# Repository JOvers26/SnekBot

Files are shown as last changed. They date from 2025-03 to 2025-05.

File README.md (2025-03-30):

# SnekBot

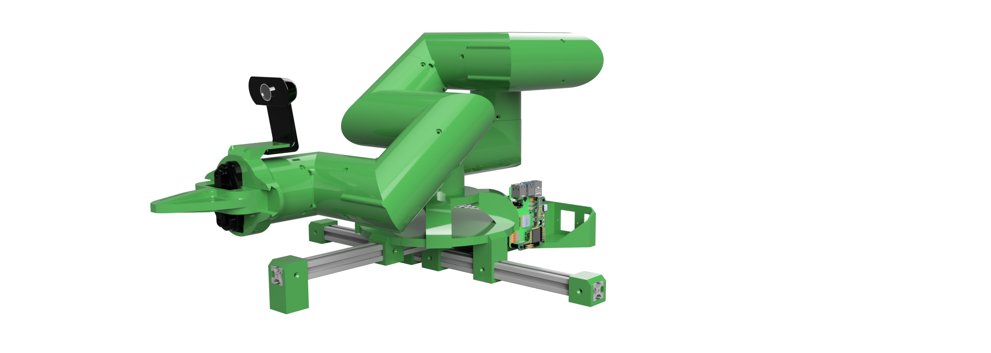
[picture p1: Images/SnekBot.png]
SnekBot Arm


## Six-Axis Robotic Arm and Control System for ROAR Lunar Surface Operations
This project is a work in progress and setup is subject to change.

## Project Summary
SnekBot is a six-axis robotic arm designed for the QUT ROAR team to use in the Australian Rover Challenge (ARCh)

## Installation & Setup
### Initial Steps
Ensure Ubuntu 24.04 is flashed on the Raspberry Pi 5 and configured for remote access via SSH.

## ROS2 Jazzy
### **1. Set Locale**
Ensure your system uses **UTF-8** encoding:
```sh
locale  # Check for UTF-8

sudo apt update && sudo apt install locales
sudo locale-gen en_US en_US.UTF-8
sudo update-locale LC_ALL=en_US.UTF-8 LANG=en_US.UTF-8
export LANG=en_US.UTF-8

locale  # Verify settings
```

### **2. Enable Required Repositories**
```sh
sudo apt install software-properties-common
sudo add-apt-repository universe
```

### **3. Add ROS 2 GPG Key**
```sh
sudo apt update && sudo apt install curl -y
sudo curl -sSL https://raw.githubusercontent.com/ros/rosdistro/master/ros.key -o /usr/share/keyrings/ros-archive-keyring.gpg
```

### **4. Add ROS 2 Repository**
```sh
echo "deb [arch=$(dpkg --print-architecture) signed-by=/usr/share/keyrings/ros-archive-keyring.gpg] http://packages.ros.org/ros2/ubuntu $(. /etc/os-release && echo $UBUNTU_CODENAME) main" | sudo tee /etc/apt/sources.list.d/ros2.list > /dev/null
```

### **5. Install Development Tools (Optional)**
```sh
sudo apt update && sudo apt install ros-dev-tools
```

### **6. Update Repository Caches**
```sh
sudo apt update
```

### **7. Upgrade System**
```sh
sudo apt upgrade
```

### **8. Install ROS 2 Jazzy Base**
```sh
sudo apt install ros-jazzy-ros-base
```

### **9. Setup Environment**
Ensure ROS 2 is sourced correctly:
```sh
# Replace ".bash" with your shell if you're not using Bash
# Possible values: setup.bash, setup.sh, setup.zsh
source /opt/ros/jazzy/setup.bash
```
For more details, visit the [official ROS 2 documentation](https://docs.ros.org/en/jazzy/Installation/Ubuntu-Install-Debs.html).

## Setting up SnekBot Project
### **1. Clone the repository**
```sh
git clone https://github.com/JOvers26/SnekBot
cd ~/SnekBot
```

### **2. Install dependencies**
```sh
cd ~/SnekBot/ros2_ws
sudo rosdep init
rosdep update
rosdep install --from-paths src --ignore-src -r -y
```

### **3. Install FOXGLOVE Monitoring (Optional)**
```sh
source /opt/ros/jazzy/setup.bash
sudo apt install ros-$ROS_DISTRO-foxglove-bridge
```

### **4. Build the ROS2 Workspace:**
```sh
cd ~SnekBot/ros2_ws
colcon build --symlink-install
source install/setup.bash
```

## Setting up ESP-IDF
### **1. Install Prerequisites**
```sh
sudo apt-get install git wget flex bison gperf python3 python3-pip python3-venv cmake ninja-build ccache libffi-dev libssl-dev dfu-util libusb-1.0-0
```

### **2. Get ESP-IDF**
```sh
mkdir -p ~/esp
cd ~/esp
git clone -b v5.2.5 --recursive https://github.com/espressif/esp-idf.git
```

### **3. Set up the Tools**
```sh
cd ~/esp/esp-idf
./install.sh all
```

### **4. Set up the Environment Variables**
```sh
. $HOME/esp/esp-idf/export.sh
```

### **5. Configure ESP32S3**
```sh
cd ~SnekBot/ESP32_Code/int32_Publisher
pip3 install catkin_pkg lark-parser colcon-common-extensions empy==3.3.4
idf.py set-target esp32s3
idf.py menuconfig

#In micro-ROS Settings ->
  #Set micro-ROS-Agent IP
  #Set WiFi Credentials
```

### **6. Build and flash software**
```sh
idf.py build
idf.py -p /dev/ttyACM0 flash

# Note if this does not work you may need to add user to the dialout group
sudo usermod -aG dialout $USER

idf.py -p /dev/ttyACM0 flash
```

## Install VSCode on Ubuntu
### **1. Install Prerequisites**
```sh
sudo apt-get install wget gpg
wget -qO- https://packages.microsoft.com/keys/microsoft.asc | gpg --dearmor > packages.microsoft.gpg
sudo install -D -o root -g root -m 644 packages.microsoft.gpg /etc/apt/keyrings/packages.microsoft.gpg
echo "deb [arch=amd64,arm64,armhf signed-by=/etc/apt/keyrings/packages.microsoft.gpg] https://packages.microsoft.com/repos/code stable main" |sudo tee /etc/apt/sources.list.d/vscode.list > /dev/null
rm -f packages.microsoft.gpg
sudo apt install apt-transport-https
sudo apt update
sudo apt install code # or code-insiders
```

## Setting up Robotics Toolbox Python environment
### **1. Install Prerequisites**
```sh
sudo apt install python3-venv
cd ~SnekBot
python3 -m venv venv
source venv/bin/activate

pip3 install pygame
pip3 install setuptools
pip3 install roboticstoolbox-python
pip3 install "numpy<2"
```

## Useful Commands
### **Sourcing Ros2**
```sh
source /opt/ros/jazzy/setup.bash
```

### **Building micro-ROS-Agent**
```sh
cd ~SnekBot/ros2_ws
colcon build --symlink-install
source install/setup.bash
```
```sh
ros2 run micro_ros_agent micro_ros_agent udp4 --port 8888
```

### **Launching Foxglove Monitoring**
```sh
source /opt/ros/jazzy/setup.bash
ros2 run foxglove_bridge foxglove_bridge
```

### **Sourcing ESP-IDF**
```sh
. $HOME/esp/esp-idf/export.sh
```

### **Flashing and Monitoring ESP32-S3**
```sh
idf.py -p /dev/ttyACM0 flash
idf.py -p /dev/ttyACM0 monitor
```

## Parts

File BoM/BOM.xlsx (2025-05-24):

Floor Mounted SnekBot
BoM Level | Part | Description | Pcs | Pcs / Unit | Unit Cost | Cost | Total Cost | Link
1 | 6813-2RS 65X85X10mm | Deep Groove Ball Bearings | 6 | 2 | $16.79 | $50.37 | $50.37 | https://www.aliexpress.com/item/1005007420073930.html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
2 | M3 x 50Pieces | M3 10mm Allen Bolt Screw | 120 | 50 | $1.57 | $3.77 | $4.71 | https://www.aliexpress.com/item/4000981220901.html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
3 | M4 x 20Pieces | M4 10mm Allen Bolt Screw | 24 | 20 | $1.57 | $1.88 | $3.14 | https://www.aliexpress.com/item/4000981220901.html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
4 | 150KG 12V DS51150 | 150Kg Servo | 6 | 1 | $32.99 | $197.94 | $197.94 | https://www.aliexpress.com/item/1005006215742647.html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
5 | ZIQIAN | 1080P Webcam | 1 | 1 | $24.89 | $24.89 | $24.89 | https://www.amazon.com.au/dp/B07VL7BNLZ?ref=ppx_yo2ov_dt_b_fed_asin_title&th=1
6 | 606-6x17x6mm | End Effector Bearings | 4 | 10 | $4.54 | $1.82 | $4.54 | https://www.aliexpress.com/item/4000909583668.html?scm_id=1007.14452.398466.0&scm-url=1007.14452.398466.0
7 | C14 Locked S8B | Power Supply Docking Outlet | 1 | 1 | $2.14 | $2.14 | $2.14 | https://www.aliexpress.com/item/1005001515720134.html?src=google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
8 | KCD3 3PIN Black | Power Supply Rocker Switch | 1 | 1 | $1.66 | $1.66 | $1.66 | https://www.aliexpress.com/item/1005005681017616.html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
9 | 12V 15A 180W | 180W Power Supply Adapter Transformer | 1 | 1 | $21.39 | $21.39 | $21.39 | https://www.amazon.com.au/dp/B0986LNBW8?ref=ppx_yo2ov_dt_b_fed_asin_title&th=1
10 | Raspberry Pi | 5 Model B 16GB | 1 | 1 | $212.50 | $212.50 | $212.50 | https://core-electronics.com.au/raspberry-pi-5-model-b-16gb.html
11 | USB C Cable | 15cm | 1 | 1 | $9.71 | $9.71 | $9.71 | https://www.amazon.com.au/dp/B01CZVEUIE?ref=ppx_yo2ov_dt_b_fed_asin_title&th=1
12 | XT60 Connectors | Male - Female Pair | 7 | 5 | $13.71 | $19.19 | $27.42 | https://www.aliexpress.com/w/wholesale-XT%2525252d60-XT60-Male-Female.html
13 | Light Duty Hook-up Wire | 26 AWG Pack | 1 | 8 | $39.95 | $4.99 | $39.95 | https://www.jaycar.com.au/light-duty-hook-up-wire-pack-8-colours/p/WH3009
14 | Power Wire (Black) | 16 AWG (5 meter) | 1 | 1 | $1.57 | $1.57 | $1.57 | https://www.aliexpress.com/item/1005006064722016.html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
15 | Power Wire (Red) | 16 AWG (5 meter) | 1 | 1 | $1.57 | $1.57 | $1.57 | https://www.aliexpress.com/item/1005006064722016.html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
16 | Dupont Connector 2.54mm | Dupont Cable Jumper Wire Pin Header Housing Kit | 1 | 1 | $1.57 | $1.57 | $1.57 | https://www.aliexpress.com/item/33011610420.html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
17 | LM2596 | DC to DC Buck Converter | 2 | 5 | $8.01 | $3.20 | $8.01 | https://www.aliexpress.com/item/1005007331564532.html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
18 | 2020 Extrusion | 450MM | 2 | 1 | $13.59 | $27.18 | $27.18 | https://www.aliexpress.com/item/1005002645411058.html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
19 | M3 x 20Pieces | 20 Series Slot T-nut Sliding T Nut | 20 | 20 | $3.49 | $3.49 | $3.49 | https://www.aliexpress.com/item/32814359094.html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
20 | 1x20kg 180 Arm | End Effector Servo Motor | 1 | 1 | $10.40 | $10.40 | $10.40 | https://www.aliexpress.com/item/1005007532136781.html?scm_id=1007.40196.436742.0&scm-url=1007.40196.436742.0
21 | 356-EP32S3WROOM1N8R8 | ESP32-S3 | 1 | 1 | $5.68 | $5.68 | $5.68 | https://au.mouser.com/ProductDetail/356-EP32S3WROOM1N8R8
22 | SKRKAHE020 | ESP32 Control Buttons | 2 | 1 | $0.91 | $1.82 | $1.82 | https://au.mouser.com/ProductDetail/688-SKRKAHE010
23 | 640-USB4105-GF-A | USBC Connector | 1 | 1 | $1.01 | $1.01 | $1.01 | https://au.mouser.com/ProductDetail/640-USB4105-GF-A
24 | 926-LM1117MPX3.3NOPB | Volatge Regulator | 1 | 1 | $1.43 | $1.43 | $1.43 | https://au.mouser.com/ProductDetail/926-LM1117MPX3.3NOPB
25 | 581-MP01EA045 | Diode | 1 | 1 | $0.83 | $0.83 | $0.83 | https://au.mouser.com/ProductDetail/581-MP01EA045
26 | 667-ERJ-UP6D5101V | 5.1KOhm Resistors | 3 | 1 | $0.23 | $0.69 | $0.69 | https://au.mouser.com/ProductDetail/667-ERJ-UP6D5101V
27 | 581-KGM21AR71A106KU | 10uF Capacitor | 2 | 1 | $0.46 | $0.93 | $0.93 | https://au.mouser.com/ProductDetail/581-KGM21AR71A106KU
28 | 963-LMK212SD104KG-T | 0.1uF Capacitor | 3 | 1 | $0.46 | $1.39 | $1.39 | https://au.mouser.com/ProductDetail/963-LMK212SD104KG-T
29 | PCD | JLCPCB | 1 | 5 | $20.00 | $4.00 | $20.00 | https://jlcpcb.com/?from=VGB_AU&adgroupid=172970581377&gad_source=1&gbraid=0AAAAACUKBgRO7FoYKeTPkvkSdP2pwtPFG
30 | eSUN PLA+ 3D Filament | 2.85mm 1kg | 2 | 1 | $25.95 | $51.90 | $51.90 | https://cubictech.com.au/products/esun-pla-3d-filament-2-85mm-1kg?variant=40317601865
30 | xbox Controller |  | 1 | 1 | $89 | $89.00 | $89.00 | https://www.amazon.com.au/Xbox-Wireless-Controller-Carbon-Black/dp/B08K3FVP5N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
Totals |  |  |  |  |  | $759.92 | $828.83
Snekbot Only |  |  |  |  |  | $439.18 | $492.09

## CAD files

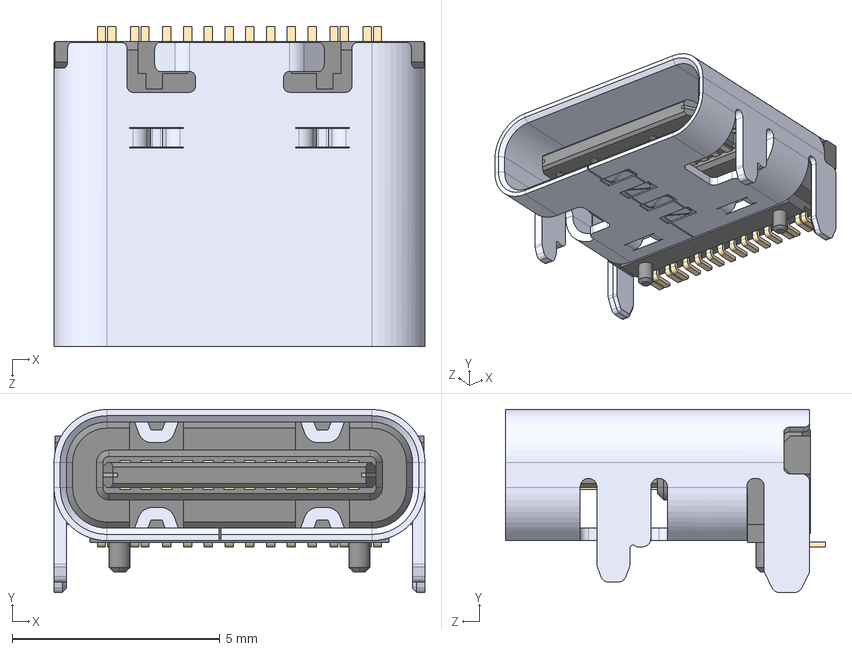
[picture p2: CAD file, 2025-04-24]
ESP32 PCB/USB4105-GF-A/USB4105-GF-A.step
8.94 x 4.41 x 7.71 mm

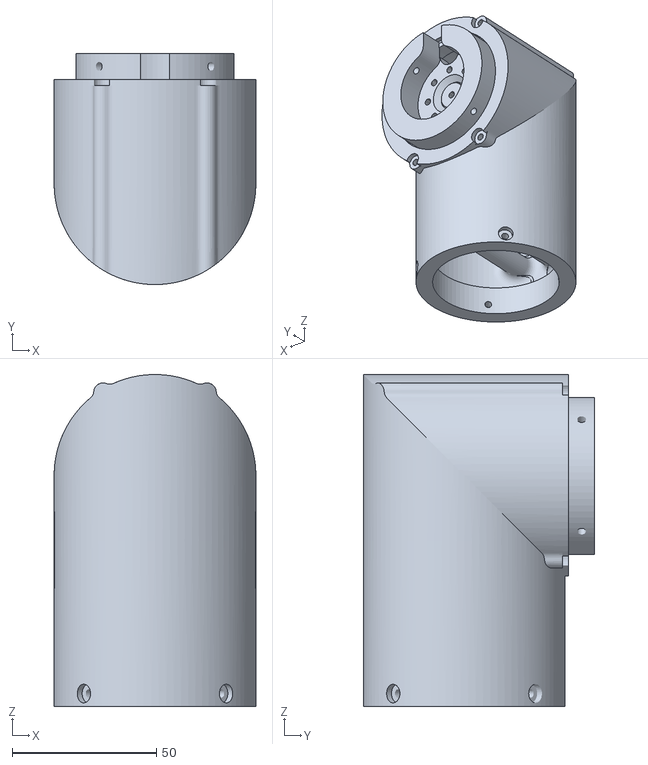
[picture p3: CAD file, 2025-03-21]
RaspberryPi_Code/SnekBot_URDF/meshes/Joint0.stl
70.0 x 80.2 x 115.2

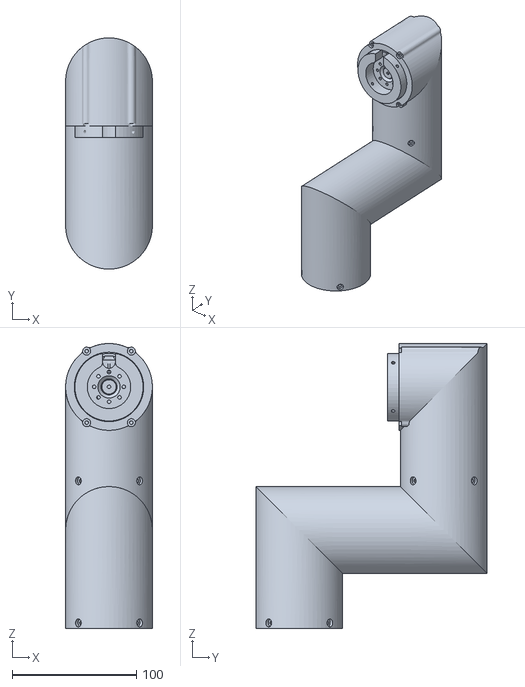
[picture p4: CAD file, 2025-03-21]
RaspberryPi_Code/SnekBot_URDF/meshes/Joint3.stl
70.0 x 186.4 x 229.8

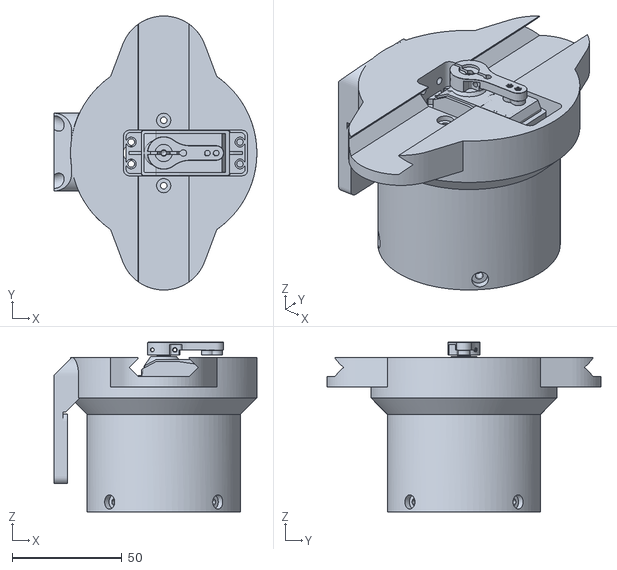
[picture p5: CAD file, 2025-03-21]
RaspberryPi_Code/SnekBot_URDF/meshes/Joint5.stl
92.5 x 125.0 x 77.4

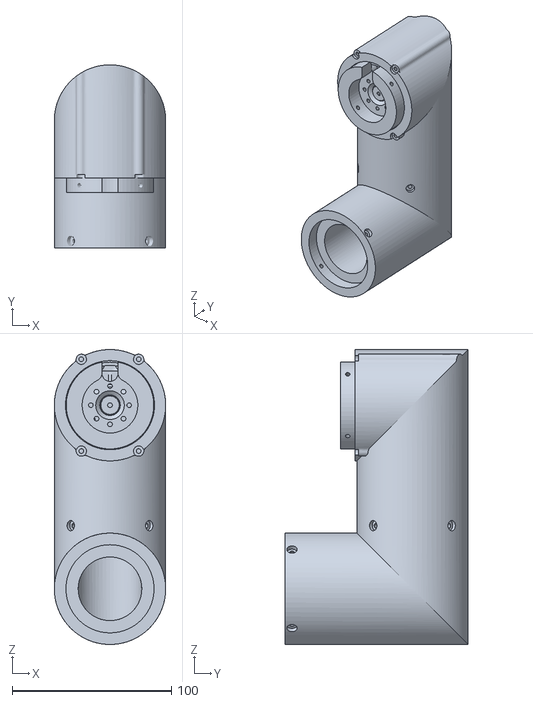
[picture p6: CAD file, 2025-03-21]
RaspberryPi_Code/SnekBot_URDF/meshes/Joint1.stl
70.0 x 115.2 x 185.4

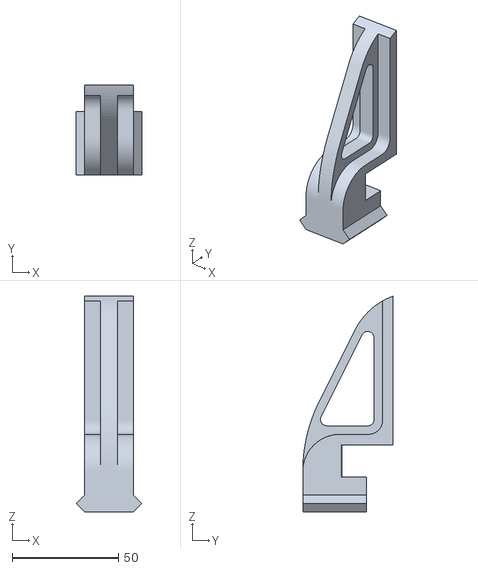
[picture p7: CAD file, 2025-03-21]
RaspberryPi_Code/SnekBot_URDF/meshes/Left-Gripper.stl
31.0 x 42.5 x 101.5

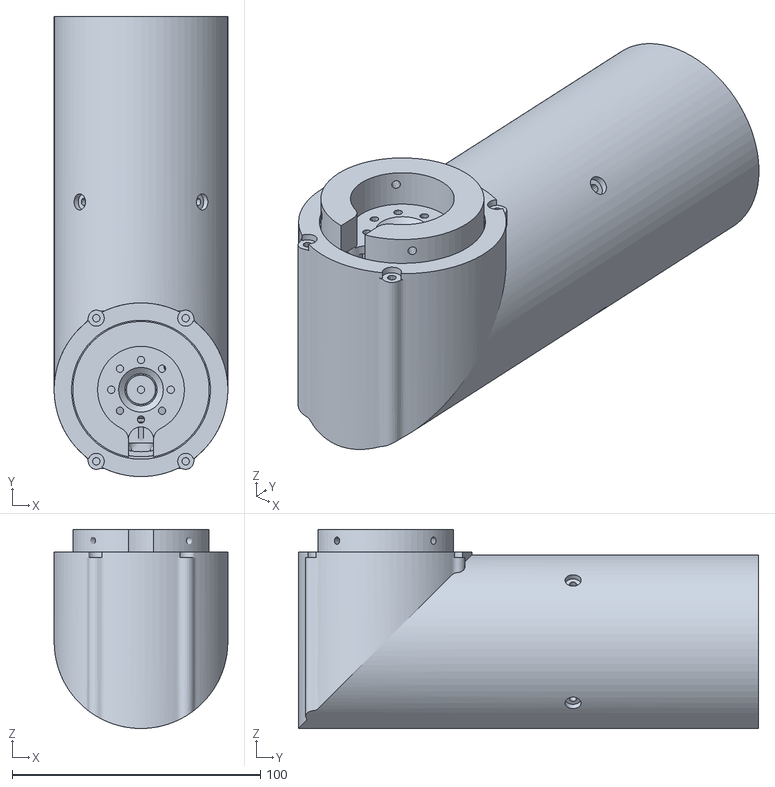
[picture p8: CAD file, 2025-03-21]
RaspberryPi_Code/SnekBot_URDF/meshes/Base.stl
70.0 x 185.5 x 80.2

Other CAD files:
RaspberryPi_Code/SnekBot_URDF/meshes/Joint2.stl
RaspberryPi_Code/SnekBot_URDF/meshes/Joint4.stl
RaspberryPi_Code/SnekBot_URDF/meshes/Right-Gripper.stl

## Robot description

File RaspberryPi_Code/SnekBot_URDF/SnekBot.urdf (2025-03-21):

<?xml version='1.0' encoding='utf-8'?>
<robot name="SnekBot">
    <link name="Joint4">
        <inertial>
            <origin xyz="-7.31917079953468e-07 -0.002720965823309811 -0.06094824846597635" rpy="0.0 9.921302603843483e-48 0.0" />
            <mass value="2.170299150249054" />
            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
        </inertial>
        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
    </link>
    <link name="Joint3">
        <inertial>
            <origin xyz="1.4095052347553083e-07 -0.06948927422346683 -0.1036765010036558" rpy="0.0 -0.0 1.302943823802202e-60" />
            <mass value="6.860254512476634" />
            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
        </inertial>
        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
    </link>
    <link name="Joint2">
        <inertial>
            <origin xyz="-7.319170719899921e-07 -0.0027209737564369975 -0.060948248465979474" rpy="3.944304526105059e-31 2.8562667779245755e-62 9.723461371658036e-63" />
            <mass value="2.170299150249074" />
            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
        </inertial>
        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
    </link>
    <link name="Joint1">
        <inertial>
            <origin xyz="3.744606777828738e-07 0.04699627745454283 -0.0685629731482273" rpy="0.0 -0.0 0.0" />
            <mass value="4.508264373489419" />
            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
        </inertial>
        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
    </link>
    <link name="Joint0">
        <inertial>
            <origin xyz="-7.319170712847745e-07 -0.002720973756436303 -0.06094825459578699" rpy="0.0 -0.0 0.0" />
            <mass value="2.1702991502490603" />
            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
        </inertial>
        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
    </link>
    <link name="Base">
        <inertial>
            <origin xyz="-4.1041387313046547e-07 -0.020138795421307955 0.037548882045009294" rpy="0.0 0.0 0.0" />
            <mass value="3.812666297852429" />
            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
        </inertial>
        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
    </link>
    <link name="Joint5">
        <inertial>
            <origin xyz="-0.0025494513129547705 -7.658363454307156e-06 -0.04525477560826317" rpy="0.0 -0.0 -1.1973985901296076e-48" />
            <mass value="1.7334916519714307" />
            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
        </inertial>
        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
    </link>
    <joint name="Base_Revolute-0" type="revolute">
        <origin xyz="-5.742377618504593e-17 -0.07946200000000023 0.035" rpy="3.141592653589793 0 0" />
        <parent link="Base" />
        <child link="Joint0" />
        <axis xyz="0 0 1" />
        <limit lower="-2.356194" upper="2.356194" effort="87" velocity="2.175" />
    </joint>
    <joint name="Joint0_Revolute-1" type="revolute">
        <origin xyz="-6.192261280341597e-50 -0.036199999999999996 -0.0802" rpy="-1.5707963267948952 0 0" />
        <parent link="Joint0" />
        <child link="Joint1" />
        <axis xyz="0 0 1" />
        <limit lower="-2.356194" upper="2.356194" effort="87" velocity="2.175" />
    </joint>
    <joint name="Joint1_Revolute-2" type="revolute">
        <origin xyz="7.592786212752303e-33 0.11539999999999996 -0.04400000000000016" rpy="-3.1415926535897922 0 0" />
        <parent link="Joint1" />
        <child link="Joint2" />
        <axis xyz="0 0 1" />
        <limit lower="-2.356194" upper="2.356194" effort="87" velocity="2.175" />
    </joint>
    <joint name="Joint2_Revolute-3" type="revolute">
        <origin xyz="5.123092549358938e-32 -0.036200000000000225 -0.08019999999999991" rpy="-1.570796326794893 0 0" />
        <parent link="Joint2" />
        <child link="Joint3" />
        <axis xyz="0 0 1" />
        <limit lower="-2.356194" upper="2.356194" effort="87" velocity="2.175" />
    </joint>
    <joint name="Joint3_Revolute-4" type="revolute">
        <origin xyz="1.1040657277305825e-14 -0.0802000000000012 -0.19479999999999947" rpy="1.5707963267948506 0 0" />
        <parent link="Joint3" />
        <child link="Joint4" />
        <axis xyz="0 0 1" />
        <limit lower="-2.356194" upper="2.356194" effort="87" velocity="2.175" />
    </joint>
    <joint name="Joint4_Revolute-5" type="revolute">
        <origin xyz="1.8787416067335387e-15 -0.036199999999996846 -0.08020000000000144" rpy="-1.570796326794869 0 0" />
        <parent link="Joint4" />
        <child link="Joint5" />
        <axis xyz="0 0 1" />
        <limit lower="-2.356194" upper="2.356194" effort="87" velocity="2.175" />
    </joint>
</robot>

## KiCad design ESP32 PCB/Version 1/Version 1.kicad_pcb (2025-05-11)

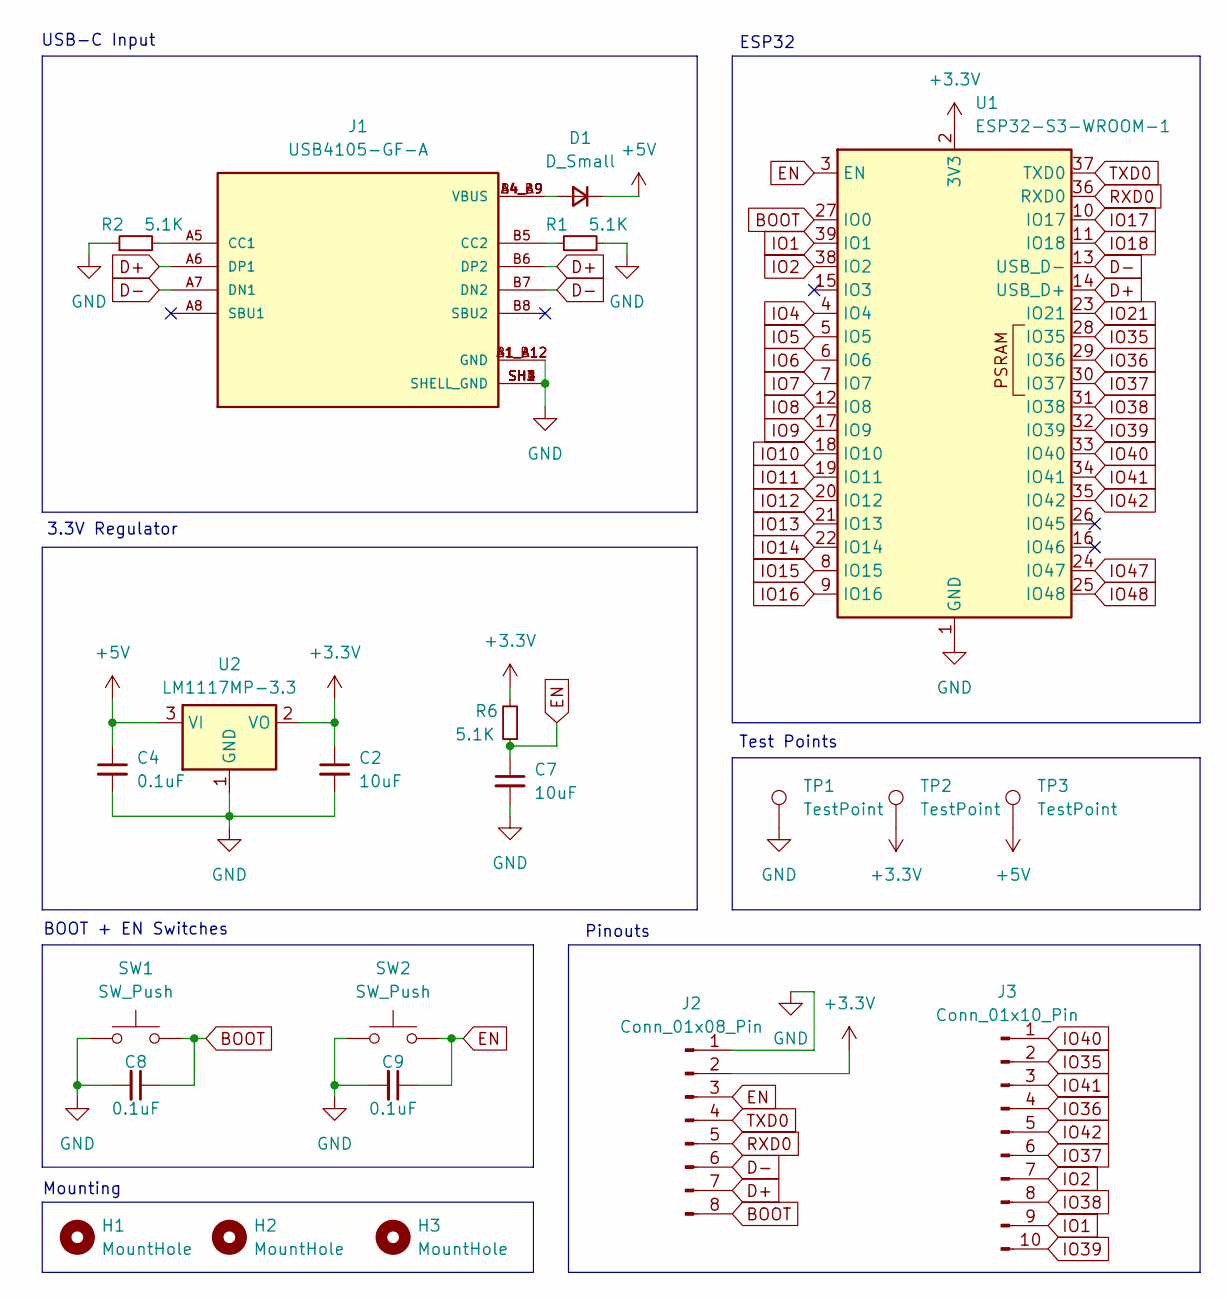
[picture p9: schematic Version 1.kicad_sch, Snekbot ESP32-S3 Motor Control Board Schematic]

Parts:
C2, C7: 10uF; C_0805_2012Metric_Pad1.18x1.45mm_HandSolder
C4, C8, C9: 0.1uF; C_0805_2012Metric_Pad1.18x1.45mm_HandSolder
D1: D_Small; D_0805_2012Metric_Pad1.15x1.40mm_HandSolder
H1, H2, H3: MountHole; MountingHole_3.2mm_M3
J1: USB4105-GF-A; GCT_USB4105-GF-A; PARTREV B4
J2: Conn_01x08_Pin; PinHeader_1x08_P2.54mm_Vertical
J3: Conn_01x10_Pin; PinHeader_2x05_P2.54mm_Vertical
R1, R2, R6: 5.1K; R_0805_2012Metric_Pad1.20x1.40mm_HandSolder
SW1, SW2: SW_Push; SW_Push_SPST_NO_Alps_SKRK
TP1, TP2, TP3: TestPoint; TestPoint_Pad_D3.0mm
U1: ESP32-S3-WROOM-1
U2: LM1117MP-3.3; SOT-223-3_TabPin2

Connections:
+3.3V: C2.1, J2.2, R6.2, TP2.1, U1.2 (3V3), U2.2 (VO)
+5V: C4.1, D1.1 (K), TP3.1, U2.3 (VI)
BOOT: C8.1, J2.8, SW1.2, U1.27 (IO0)
D+: J1.A6 (DP1), J1.B6 (DP2), J2.7, U1.14 (USB_D+)
D-: J1.A7 (DN1), J1.B7 (DN2), J2.6, U1.13 (USB_D-)
EN: C7.1, C9.1, J2.3, R6.1, SW2.2, U1.3 (EN)
GND: C2.2, C4.2, C7.2, C8.2, C9.2, J1.A1_B12 (GND), J1.B1_A12 (GND), J1.SH1 (SHELL_GND), J1.SH2 (SHELL_GND), J1.SH3 (SHELL_GND), J1.SH4 (SHELL_GND), J2.1, R1.2, R2.1, SW1.1, SW2.1, TP1.1, U1.1 (GND), U1.40 (GND), U1.41 (GND), U2.1 (GND)
IO1: J3.9, U1.39 (IO1)
IO2: J3.7, U1.38 (IO2)
IO4: U1.4 (IO4)
IO5: U1.5 (IO5)
IO6: U1.6 (IO6)
IO7: U1.7 (IO7)
IO8: U1.12 (IO8)
IO9: U1.17 (IO9)
IO10: U1.18 (IO10)
IO11: U1.19 (IO11)
IO12: U1.20 (IO12)
IO13: U1.21 (IO13)
IO14: U1.22 (IO14)
IO15: U1.8 (IO15)
IO16: U1.9 (IO16)
IO17: U1.10 (IO17)
IO18: U1.11 (IO18)
IO21: U1.23 (IO21)
IO35: J3.2, U1.28 (IO35)
IO36: J3.4, U1.29 (IO36)
IO37: J3.6, U1.30 (IO37)
IO38: J3.8, U1.31 (IO38)
IO39: J3.10, U1.32 (IO39)
IO40: J3.1, U1.33 (IO40)
IO41: J3.3, U1.34 (IO41)
IO42: J3.5, U1.35 (IO42)
IO47: U1.24 (IO47)
IO48: U1.25 (IO48)
unnamed: D1.2 (A), J1.A4_B9 (VBUS), J1.B4_A9 (VBUS)
unnamed: J1.A5 (CC1), R2.2
unnamed: J1.B5 (CC2), R1.1
RXD0: J2.5, U1.36 (RXD0)
TXD0: J2.4, U1.37 (TXD0)

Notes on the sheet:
BOOT + EN Switches
3.3V Regulator
Mounting
Pinouts
USB-C Input
ESP32
Test Points

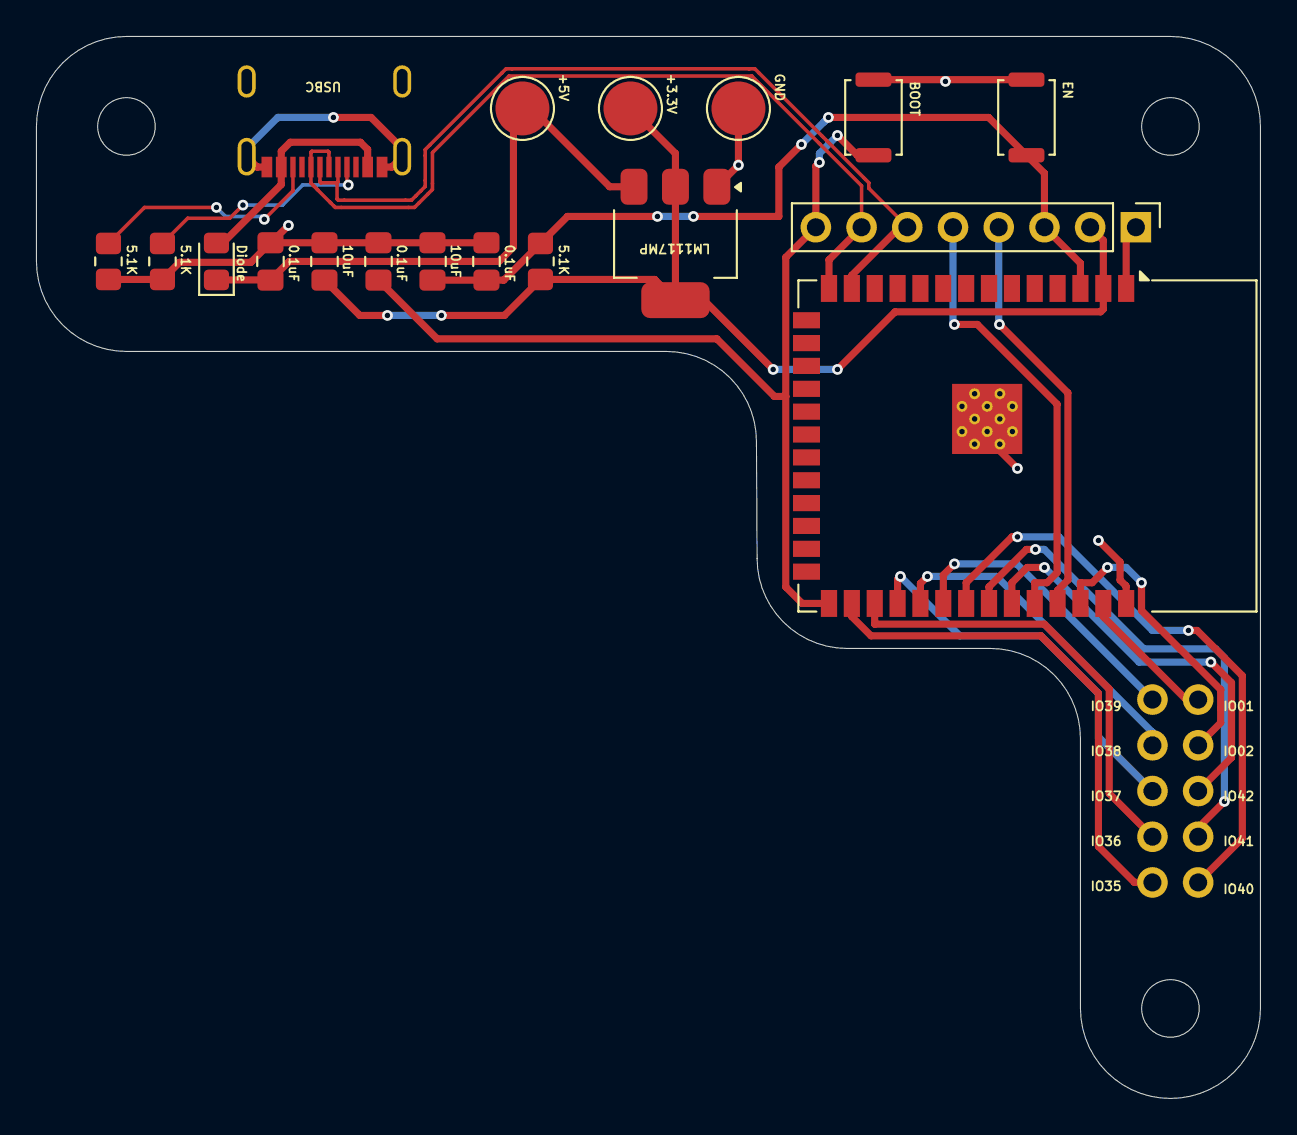
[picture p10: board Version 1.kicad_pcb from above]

Board: 2 copper layers, 68.0 x 59.0 mm, 22 parts (0 on the bottom side), 22 nets.

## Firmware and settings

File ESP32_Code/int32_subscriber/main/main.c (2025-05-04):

#include <string.h>
#include <stdio.h>
#include <unistd.h>
#include <stdlib.h>  // For malloc

#include "freertos/FreeRTOS.h"
#include "freertos/task.h"
#include "esp_log.h"
#include "esp_system.h"

#include <uros_network_interfaces.h>
#include <rcl/rcl.h>
#include <rcl/error_handling.h>
#include <sensor_msgs/msg/joint_state.h>
#include <rclc/rclc.h>
#include <rclc/executor.h>

#include "driver/mcpwm_prelude.h"
#include <math.h>

#ifdef CONFIG_MICRO_ROS_ESP_XRCE_DDS_MIDDLEWARE
#include <rmw_microros/rmw_microros.h>
#endif

#define NUM_JOINTS 7
#define RCCHECK(fn) { rcl_ret_t temp_rc = fn; if((temp_rc != RCL_RET_OK)){printf("Failed status on line %d: %d. Aborting.\n", __LINE__, (int)temp_rc); vTaskDelete(NULL);} }
#define RCSOFTCHECK(fn) { rcl_ret_t temp_rc = fn; if((temp_rc != RCL_RET_OK)){printf("Failed status on line %d: %d. Continuing.\n", __LINE__, (int)temp_rc);} }

// Subscription variable
rcl_subscription_t snekbot_joint_state_subscriber;
sensor_msgs__msg__JointState recv_joint_state_msg;

#define JOINT_1 1
#define JOINT_2 2
#define JOINT_3 42
#define JOINT_4 41
#define JOINT_5 40
#define JOINT_6 39
#define JOINT_G 38
#define SERVO_MIN_PULSEWIDTH_US 500 
#define SERVO_MAX_PULSEWIDTH_US 2500
#define SERVO_MAX_DEGREE 270
#define PI 3.14159265359

mcpwm_timer_handle_t timer0;
mcpwm_oper_handle_t operator0;
mcpwm_cmpr_handle_t comparator01;
mcpwm_cmpr_handle_t comparator02;
mcpwm_gen_handle_t generator01;
mcpwm_gen_handle_t generator02;

mcpwm_timer_handle_t timer1;
mcpwm_oper_handle_t operator1;
mcpwm_cmpr_handle_t comparator11;
mcpwm_cmpr_handle_t comparator12;
mcpwm_gen_handle_t generator11;
mcpwm_gen_handle_t generator12;

mcpwm_timer_handle_t timer2;
mcpwm_oper_handle_t operator2;
mcpwm_cmpr_handle_t comparator21;
mcpwm_cmpr_handle_t comparator22;
mcpwm_gen_handle_t generator21;
mcpwm_gen_handle_t generator22;

mcpwm_timer_handle_t timer3;
mcpwm_oper_handle_t operator3;
mcpwm_cmpr_handle_t comparator31;
mcpwm_gen_handle_t generator31;




static uint32_t radians_to_angle(float radians) {
    float angle = ((radians + M_PI) / (2 * M_PI)) * SERVO_MAX_DEGREE;
    
    if (angle < 0) angle = 0;
    if (angle > SERVO_MAX_DEGREE) angle = SERVO_MAX_DEGREE;
    
    return (uint32_t)angle;
}

static uint32_t angle_to_pulsewidth(uint32_t angle) {
    return SERVO_MIN_PULSEWIDTH_US + (angle * (SERVO_MAX_PULSEWIDTH_US - SERVO_MIN_PULSEWIDTH_US) / SERVO_MAX_DEGREE);
}

static void set_servo_angle_radians(mcpwm_cmpr_handle_t comparator, float radians) {
    uint32_t angle = radians_to_angle(radians);
    uint32_t pulse_width = angle_to_pulsewidth(angle);
    mcpwm_comparator_set_compare_value(comparator, pulse_width);
}

static void setup_pwm(void) {
    // Timer 0 setup (for JOINT_1, JOINT_2, JOINT_3)
    mcpwm_timer_config_t timer_config = {
        .group_id = 0,
        .clk_src = MCPWM_TIMER_CLK_SRC_DEFAULT,
        .resolution_hz = 1000000,  
        .count_mode = MCPWM_TIMER_COUNT_MODE_UP,
        .period_ticks = 20000  // 50Hz PWM
    };



    mcpwm_new_timer(&timer_config, &timer0);

    // Timer 1 setup (for JOINT_4, JOINT_5)
    mcpwm_new_timer(&timer_config, &timer1);

    // Timer 2 setup (for JOINT_6, JOINT_G)
    mcpwm_new_timer(&timer_config, &timer2);

    mcpwm_timer_config_t timer_config3 = {
        .group_id = 1,
        .clk_src = MCPWM_TIMER_CLK_SRC_DEFAULT,
        .resolution_hz = 1000000,  
        .count_mode = MCPWM_TIMER_COUNT_MODE_UP,
        .period_ticks = 20000  // 50Hz PWM
    };
    mcpwm_new_timer(&timer_config3, &timer3);

    // Operator setup for Timer 0
    mcpwm_operator_config_t operator_config = {.group_id = 0};
    mcpwm_new_operator(&operator_config, &operator0);
    mcpwm_operator_connect_timer(operator0, timer0);

    // Operator setup for Timer 1
    mcpwm_new_operator(&operator_config, &operator1);
    mcpwm_operator_connect_timer(operator1, timer1);

    // Operator setup for Timer 2
    mcpwm_new_operator(&operator_config, &operator2);
    mcpwm_operator_connect_timer(operator2, timer2);

    mcpwm_operator_config_t operator_config3 = {.group_id = 1};
    mcpwm_new_operator(&operator_config3, &operator3);
    mcpwm_operator_connect_timer(operator3, timer3);

    // Comparator and generator setup for each joint and timer

    // Timer 0 (for JOINT_1, JOINT_2, JOINT_3)
    // JOINT_1
    mcpwm_comparator_config_t comparator01_config = {.flags.update_cmp_on_tez = true};
    mcpwm_new_comparator(operator0, &comparator01_config, &comparator01);
    mcpwm_generator_config_t generator01_config = {
        .gen_gpio_num = JOINT_1,
        .flags.invert_pwm = false
    };
    mcpwm_new_generator(operator0, &generator01_config, &generator01);
    mcpwm_generator_set_action_on_timer_event(generator01,
        MCPWM_GEN_TIMER_EVENT_ACTION(MCPWM_TIMER_DIRECTION_UP, MCPWM_TIMER_EVENT_EMPTY, MCPWM_GEN_ACTION_HIGH));
    mcpwm_generator_set_action_on_compare_event(generator01,
        MCPWM_GEN_COMPARE_EVENT_ACTION(MCPWM_TIMER_DIRECTION_UP, comparator01, MCPWM_GEN_ACTION_LOW));

    // JOINT_2
    mcpwm_comparator_config_t comparator02_config = {.flags.update_cmp_on_tez = true};
    mcpwm_new_comparator(operator0, &comparator02_config, &comparator02);
    mcpwm_generator_config_t generator02_config = {
        .gen_gpio_num = JOINT_2,
        .flags.invert_pwm = false
    };
    mcpwm_new_generator(operator0, &generator02_config, &generator02);
    mcpwm_generator_set_action_on_timer_event(generator02,
        MCPWM_GEN_TIMER_EVENT_ACTION(MCPWM_TIMER_DIRECTION_UP, MCPWM_TIMER_EVENT_EMPTY, MCPWM_GEN_ACTION_HIGH));
    mcpwm_generator_set_action_on_compare_event(generator02,
        MCPWM_GEN_COMPARE_EVENT_ACTION(MCPWM_TIMER_DIRECTION_UP, comparator02, MCPWM_GEN_ACTION_LOW));


    // Timer 1 (for JOINT_4, JOINT_5)
    // JOINT_3
    mcpwm_comparator_config_t comparator11_config = {.flags.update_cmp_on_tez = true};
    mcpwm_new_comparator(operator1, &comparator11_config, &comparator11);
    mcpwm_generator_config_t generator11_config = {
        .gen_gpio_num = JOINT_3,
        .flags.invert_pwm = false
    };
    mcpwm_new_generator(operator1, &generator11_config, &generator11);
    mcpwm_generator_set_action_on_timer_event(generator11,
        MCPWM_GEN_TIMER_EVENT_ACTION(MCPWM_TIMER_DIRECTION_UP, MCPWM_TIMER_EVENT_EMPTY, MCPWM_GEN_ACTION_HIGH));
    mcpwm_generator_set_action_on_compare_event(generator11,
        MCPWM_GEN_COMPARE_EVENT_ACTION(MCPWM_TIMER_DIRECTION_UP, comparator11, MCPWM_GEN_ACTION_LOW));

    // JOINT_4
    mcpwm_comparator_config_t comparator12_config = {.flags.update_cmp_on_tez = true};
    mcpwm_new_comparator(operator1, &comparator12_config, &comparator12);
    mcpwm_generator_config_t generator12_config = {
        .gen_gpio_num = JOINT_4,
        .flags.invert_pwm = false
    };
    mcpwm_new_generator(operator1, &generator12_config, &generator12);
    mcpwm_generator_set_action_on_timer_event(generator12,
        MCPWM_GEN_TIMER_EVENT_ACTION(MCPWM_TIMER_DIRECTION_UP, MCPWM_TIMER_EVENT_EMPTY, MCPWM_GEN_ACTION_HIGH));
    mcpwm_generator_set_action_on_compare_event(generator12,
        MCPWM_GEN_COMPARE_EVENT_ACTION(MCPWM_TIMER_DIRECTION_UP, comparator12, MCPWM_GEN_ACTION_LOW));

    // Timer 2 (for JOINT_6, JOINT_G)
    // JOINT_5
    mcpwm_comparator_config_t comparator21_config = {.flags.update_cmp_on_tez = true};
    mcpwm_new_comparator(operator2, &comparator21_config, &comparator21);
    mcpwm_generator_config_t generator21_config = {
        .gen_gpio_num = JOINT_5,
        .flags.invert_pwm = false
    };
    mcpwm_new_generator(operator2, &generator21_config, &generator21);
    mcpwm_generator_set_action_on_timer_event(generator21,
        MCPWM_GEN_TIMER_EVENT_ACTION(MCPWM_TIMER_DIRECTION_UP, MCPWM_TIMER_EVENT_EMPTY, MCPWM_GEN_ACTION_HIGH));
    mcpwm_generator_set_action_on_compare_event(generator21,
        MCPWM_GEN_COMPARE_EVENT_ACTION(MCPWM_TIMER_DIRECTION_UP, comparator21, MCPWM_GEN_ACTION_LOW));

    // JOINT_6 (Gripper)
    mcpwm_comparator_config_t comparator22_config = {.flags.update_cmp_on_tez = true};
    mcpwm_new_comparator(operator2, &comparator22_config, &comparator22);
    mcpwm_generator_config_t generator22_config = {
        .gen_gpio_num = JOINT_6,
        .flags.invert_pwm = false
    };
    mcpwm_new_generator(operator2, &generator22_config, &generator22);
    mcpwm_generator_set_action_on_timer_event(generator22,
        MCPWM_GEN_TIMER_EVENT_ACTION(MCPWM_TIMER_DIRECTION_UP, MCPWM_TIMER_EVENT_EMPTY, MCPWM_GEN_ACTION_HIGH));
    mcpwm_generator_set_action_on_compare_event(generator22,
        MCPWM_GEN_COMPARE_EVENT_ACTION(MCPWM_TIMER_DIRECTION_UP, comparator22, MCPWM_GEN_ACTION_LOW));

    mcpwm_comparator_config_t comparator31_config = {.flags.update_cmp_on_tez = true};
    mcpwm_new_comparator(operator3, &comparator31_config, &comparator31);
    mcpwm_generator_config_t generator31_config = {
        .gen_gpio_num = JOINT_G,
        .flags.invert_pwm = false
    };
    mcpwm_new_generator(operator3, &generator31_config, &generator31);
    mcpwm_generator_set_action_on_timer_event(generator31,
        MCPWM_GEN_TIMER_EVENT_ACTION(MCPWM_TIMER_DIRECTION_UP, MCPWM_TIMER_EVENT_EMPTY, MCPWM_GEN_ACTION_HIGH));
    mcpwm_generator_set_action_on_compare_event(generator31,
        MCPWM_GEN_COMPARE_EVENT_ACTION(MCPWM_TIMER_DIRECTION_UP, comparator31, MCPWM_GEN_ACTION_LOW));

    // Start all timers
    mcpwm_timer_enable(timer0);
    mcpwm_timer_start_stop(timer0, MCPWM_TIMER_START_NO_STOP);
    
    mcpwm_timer_enable(timer1);
    mcpwm_timer_start_stop(timer1, MCPWM_TIMER_START_NO_STOP);
    
    mcpwm_timer_enable(timer2);
    mcpwm_timer_start_stop(timer2, MCPWM_TIMER_START_NO_STOP);

    mcpwm_timer_enable(timer3);
    mcpwm_timer_start_stop(timer3, MCPWM_TIMER_START_NO_STOP);
}


// Subscription callback function
void snekbot_joint_state_callback(const void * msgin)
{
    const sensor_msgs__msg__JointState * msg = (const sensor_msgs__msg__JointState *)msgin;

    if (msg == NULL) {
        printf("[ERROR] Received NULL message!\n");
        return;
    }

    printf("Received Joint States:\n");
    for (size_t i = 0; i < msg->position.size; i++) {
        printf("  Joint %zu (%s): %f\n", i, msg->name.data[i].data, msg->position.data[i]);
        if (strcmp(msg->name.data[i].data, "joint_1") == 0) {
            set_servo_angle_radians(comparator01, (float)msg->position.data[i]);
        }
        else if (strcmp(msg->name.data[i].data, "joint_2") == 0) {
            set_servo_angle_radians(comparator02, (float)msg->position.data[i]);
        }
        else if (strcmp(msg->name.data[i].data, "joint_3") == 0) {
            set_servo_angle_radians(comparator11, (float)msg->position.data[i]);
        }
        else if (strcmp(msg->name.data[i].data, "joint_4") == 0) {
            set_servo_angle_radians(comparator12, (float)msg->position.data[i]);
        }
        else if (strcmp(msg->name.data[i].data, "joint_5") == 0) {
            set_servo_angle_radians(comparator21, (float)msg->position.data[i]);
        }
        else if (strcmp(msg->name.data[i].data, "joint_6") == 0) {
            set_servo_angle_radians(comparator22, (float)msg->position.data[i]);
        }
        else if (strcmp(msg->name.data[i].data, "gripper") == 0) {
            set_servo_angle_radians(comparator31, (float)msg->position.data[i]);
        }
        
    }
}

// Micro-ROS task to handle subscriptions and execution loop
void micro_ros_task(void * arg)
{
    rcl_allocator_t allocator = rcl_get_default_allocator();
    rclc_support_t support;

    // Initialize RCL options
    rcl_init_options_t init_options = rcl_get_zero_initialized_init_options();
    RCCHECK(rcl_init_options_init(&init_options, allocator));

#ifdef CONFIG_MICRO_ROS_ESP_XRCE_DDS_MIDDLEWARE
    rmw_init_options_t* rmw_options = rcl_init_options_get_rmw_init_options(&init_options);
    RCCHECK(rmw_uros_options_set_udp_address(CONFIG_MICRO_ROS_AGENT_IP, CONFIG_MICRO_ROS_AGENT_PORT, rmw_options));
#endif

    // Initialize RCL support
    RCCHECK(rclc_support_init_with_options(&support, 0, NULL, &init_options, &allocator));

    // Create the ROS node
    rcl_node_t node = rcl_get_zero_initialized_node();
    RCCHECK(rclc_node_init_default(&node, "snekbot_joint_state_subscriber_rclc", "", &support));

    // Initialize subscription for SnekBot joint states
    RCCHECK(rclc_subscription_init_default(
        &snekbot_joint_state_subscriber,
        &node,
        ROSIDL_GET_MSG_TYPE_SUPPORT(sensor_msgs, msg, JointState),
        "snekbot/joint_states"));

    // Allocate memory for received message
    recv_joint_state_msg.position.capacity = NUM_JOINTS;
    recv_joint_state_msg.position.size = 0;
    recv_joint_state_msg.position.data = malloc(NUM_JOINTS * sizeof(double));
    
    recv_joint_state_msg.name.capacity = NUM_JOINTS;
    recv_joint_state_msg.name.size = 0;
    recv_joint_state_msg.name.data = malloc(NUM_JOINTS * sizeof(rosidl_runtime_c__String));
    
    for (size_t i = 0; i < NUM_JOINTS; i++) {
        recv_joint_state_msg.name.data[i].data = malloc(20);
        recv_joint_state_msg.name.data[i].size = 0;
        recv_joint_state_msg.name.data[i].capacity = 20;
    }

    if (!recv_joint_state_msg.position.data || !recv_joint_state_msg.name.data) {
        printf("[ERROR] Failed to allocate memory for received message\n");
        return;
    }

    // Create executor for the subscription
    rclc_executor_t executor = rclc_executor_get_zero_initialized_executor();
    RCCHECK(rclc_executor_init(&executor, &support.context, 1, &allocator));

    // Add subscription to executor
    RCCHECK(rclc_executor_add_subscription(&executor, &snekbot_joint_state_subscriber, &recv_joint_state_msg, &snekbot_joint_state_callback, ON_NEW_DATA));

    printf("Micro-ROS subscriber is running...\n");

    // Spin to handle callbacks
    while (1) {
        rclc_executor_spin_some(&executor, RCL_MS_TO_NS(10));
        usleep(10000);
    }

    // Clean up
    RCCHECK(rcl_subscription_fini(&snekbot_joint_state_subscriber, &node));
    RCCHECK(rcl_node_fini(&node));

    free(recv_joint_state_msg.position.data);
    for (size_t i = 0; i < NUM_JOINTS; i++) {
        free(recv_joint_state_msg.name.data[i].data);
    }
    free(recv_joint_state_msg.name.data);

    vTaskDelete(NULL);
}

void app_main(void)
{
    setup_pwm();
    // Initialize network interface
#if defined(CONFIG_MICRO_ROS_ESP_NETIF_WLAN) || defined(CONFIG_MICRO_ROS_ESP_NETIF_ENET)
    ESP_ERROR_CHECK(uros_network_interface_initialize());
#endif

    xTaskCreate(micro_ros_task,
                "uros_task",
                8 * 1024,
                NULL,
                CONFIG_MICRO_ROS_APP_TASK_PRIO,
                NULL);
}

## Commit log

2025-03-27 remove esp-idf
    [anti_rollback_partition.csv, cmn_crt_authorities.csv, esp_efuse_custom_table.csv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]
2025-03-30 add subscriber
    [Base.stl, Joint0.stl, Joint1.stl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]
2025-03-30 joint_states not working :(
    [main.c]
2025-04-25 joint0 manipulation
2025-05-04 Removed code that is now invalid
    [BOM.xlsx]
